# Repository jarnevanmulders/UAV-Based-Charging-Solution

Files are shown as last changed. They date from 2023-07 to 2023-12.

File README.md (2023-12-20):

# UAV Based Charging Solution

- [NRF52832 DK pinout](https://os.mbed.com/platforms/Nordic-nRF52-DK/)
- [NRF52832 DK schematics](https://devzone.nordicsemi.com/cfs-file/__key/communityserver-discussions-components-files/4/PCA10040_5F00_Schematic_5F00_And_5F00_PCB.pdf)

# HW design
- [BLE 2.4GHz antenna design](https://www.infineon.com/dgdl/Infineon-AN91445_Antenna_Design_and_RF_Layout_Guidelines-ApplicationNotes-v09_00-EN.pdf)

# Image hardware
Image measurement setup

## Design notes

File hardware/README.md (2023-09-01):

# Hardware status
## PRU
Working

Updates from v1.0 to v1.1
- I2C programmable load
- VDD_BLE directly connected to ADC pin P03 (without voltage divider)
- Additional RC filter after current limiter OPAMP
- Button from pull-up to pull down
- Additional filter (ferrite bead) on VDD_BLE supply line
- Other load switch implementation (with dual PMOS PMDPB55XP)
- Diode and shunt resistor location changed
- MIFA antenna tuning
  - Measured impedance 25+j25
    - Measured with R&S ZVL 3GHz VNA
    - Used a calibrated UFL connector cable (calibrated with ZVL one port calibration procedure)
    - Blank PCB board was used for measurement
  - Added 1.2 pF parallel with antenna (as compensation (see Smith V4.1))
  - Total [Pi] matching circuit (MCU - 0.8 pF capacitor - 3.9 nH inductor - 1.2 pF capacitor)

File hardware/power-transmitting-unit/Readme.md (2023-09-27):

## Hardware status

## Architecture
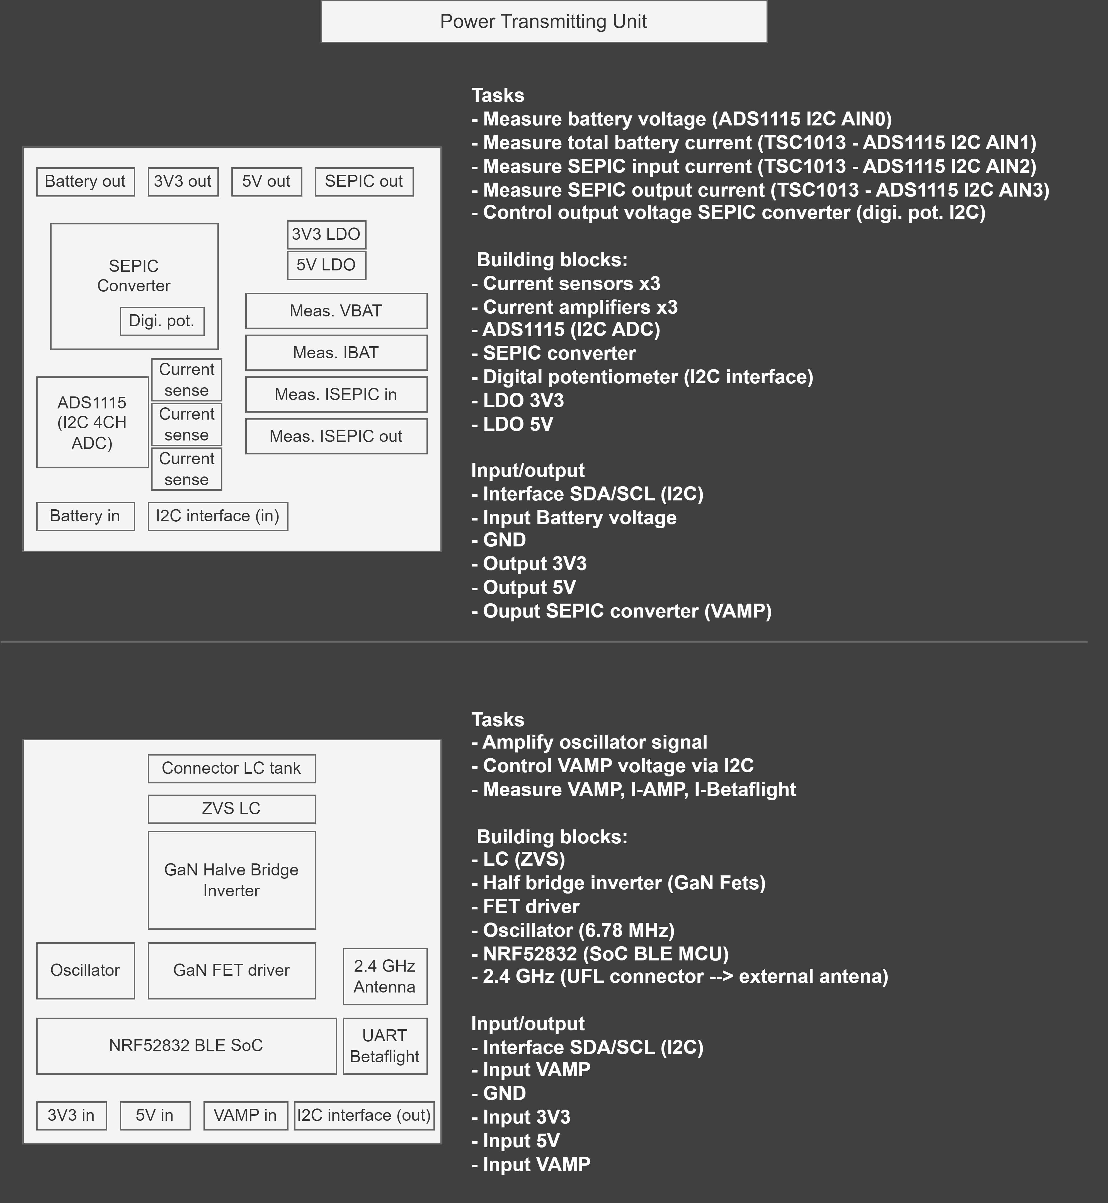
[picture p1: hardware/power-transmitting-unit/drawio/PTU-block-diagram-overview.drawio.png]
architecture


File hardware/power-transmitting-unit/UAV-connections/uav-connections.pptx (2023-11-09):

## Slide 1

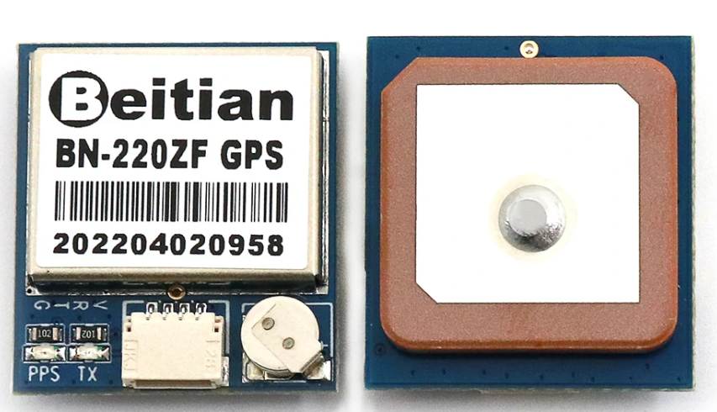
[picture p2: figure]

T1 – green
R1 – white
GND – black
5V – red

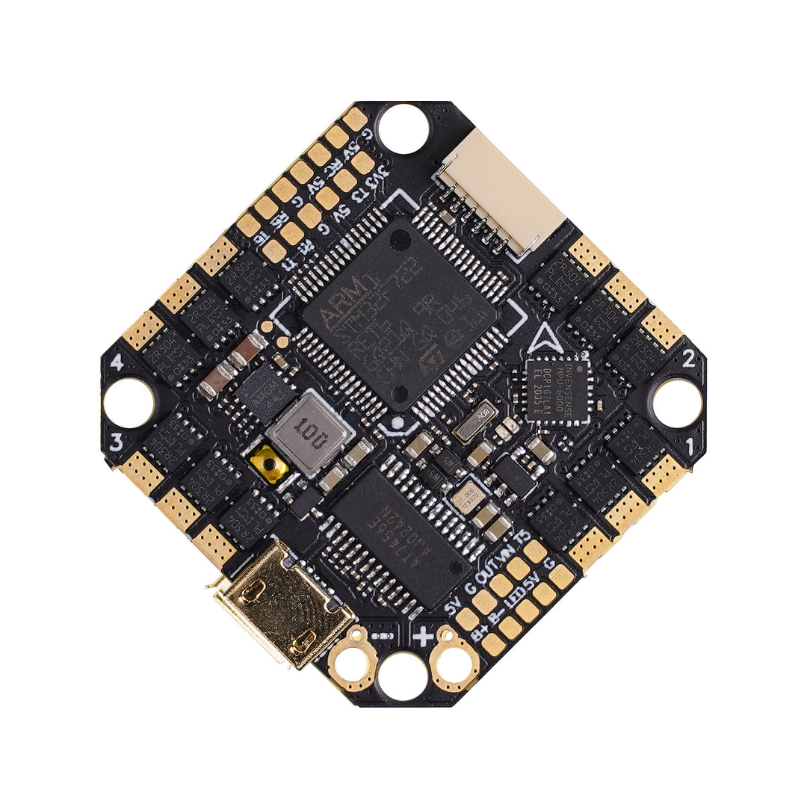
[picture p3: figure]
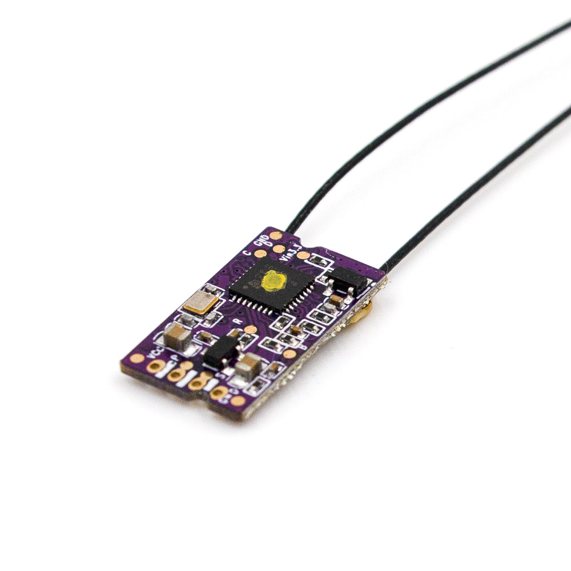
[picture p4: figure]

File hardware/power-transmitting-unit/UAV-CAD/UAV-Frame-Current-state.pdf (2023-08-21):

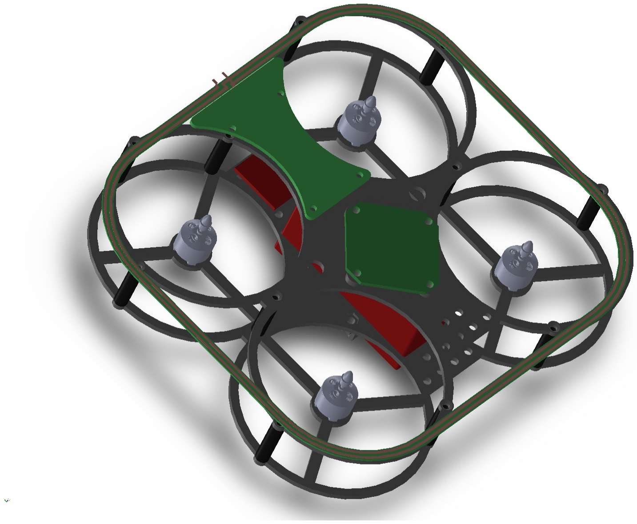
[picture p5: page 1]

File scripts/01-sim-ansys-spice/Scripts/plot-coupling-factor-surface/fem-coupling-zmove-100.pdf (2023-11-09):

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

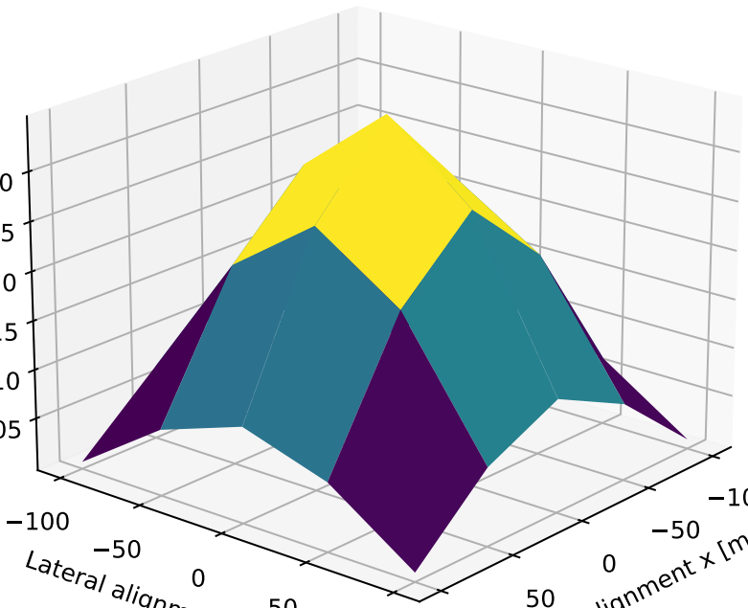
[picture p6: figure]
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

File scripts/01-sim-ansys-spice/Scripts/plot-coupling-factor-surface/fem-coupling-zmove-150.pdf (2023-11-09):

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

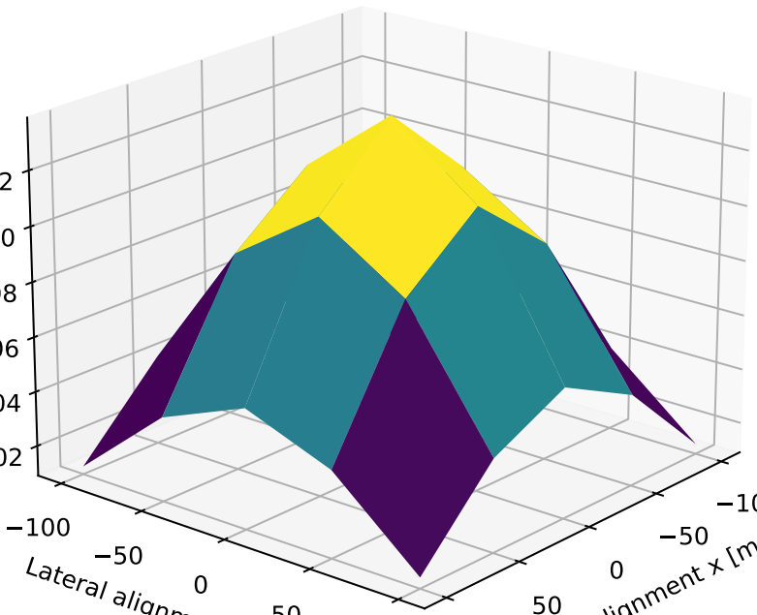
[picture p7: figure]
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

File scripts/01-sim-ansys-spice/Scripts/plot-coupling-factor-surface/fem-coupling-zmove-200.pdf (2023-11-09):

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

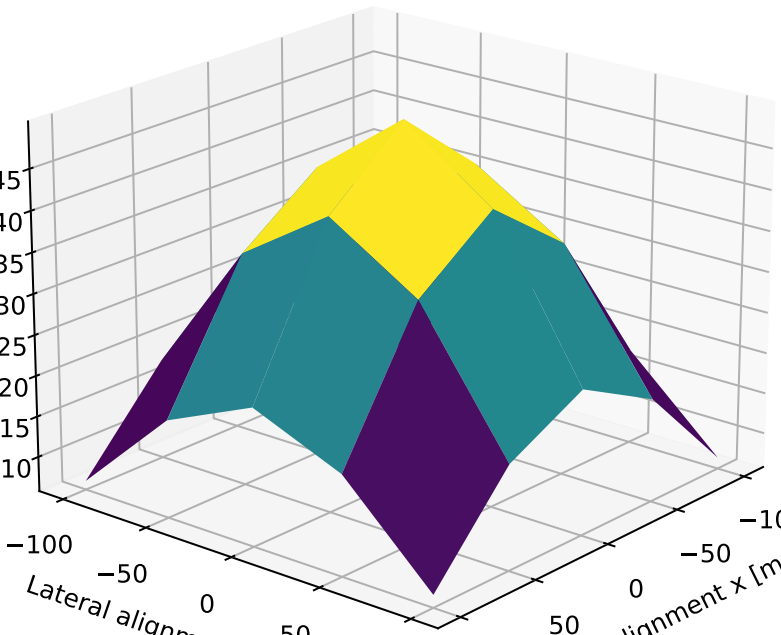
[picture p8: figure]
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

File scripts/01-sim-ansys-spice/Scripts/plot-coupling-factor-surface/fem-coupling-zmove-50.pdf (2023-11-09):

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

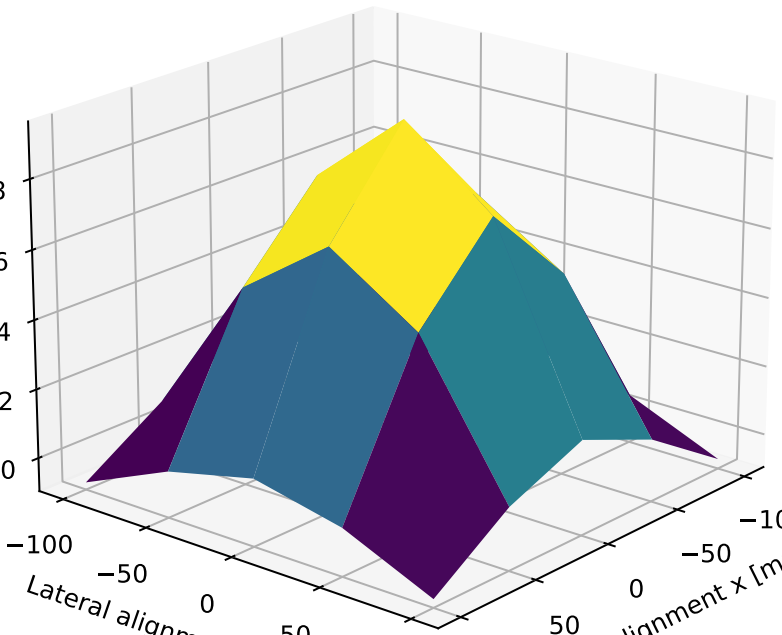
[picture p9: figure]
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

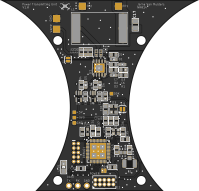
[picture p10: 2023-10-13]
hardware/power-transmitting-unit/Eagle-CAD/PTU-board/SVG-renders-design-1/top.png

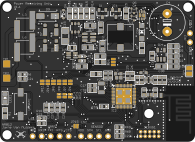
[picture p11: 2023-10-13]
hardware/power-receiving-unit/SVG-renders-design1-1/top.png

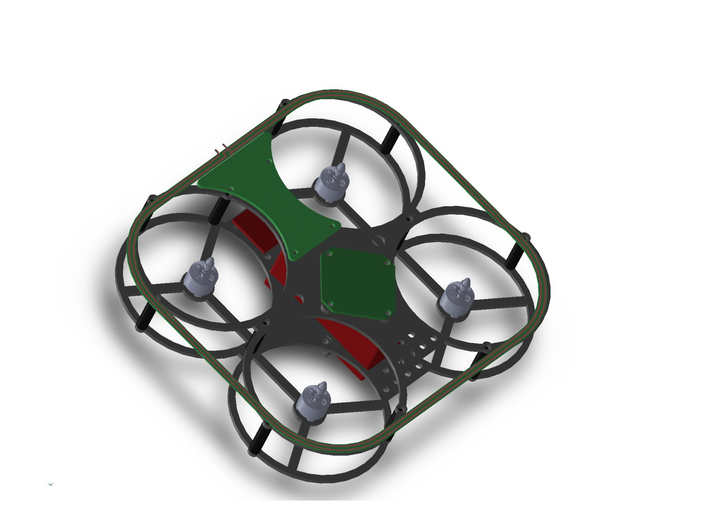
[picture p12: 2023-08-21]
hardware/power-transmitting-unit/UAV-CAD/UAV-Frame-Current-state-1.png

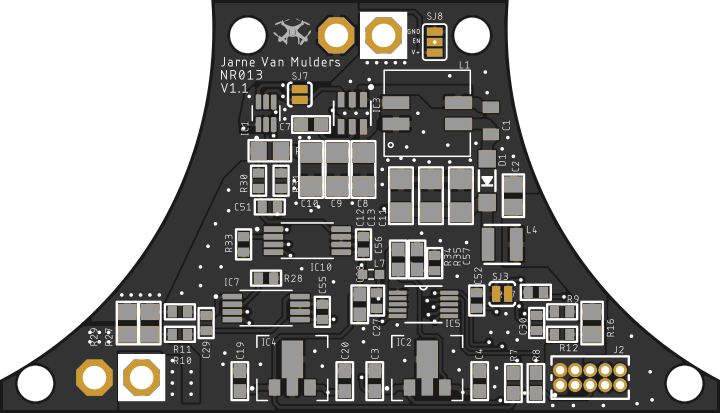
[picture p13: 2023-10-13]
hardware/power-transmitting-unit/Eagle-CAD/PSU-board/version-1-1/SVG-renders-design-1-1/top.png

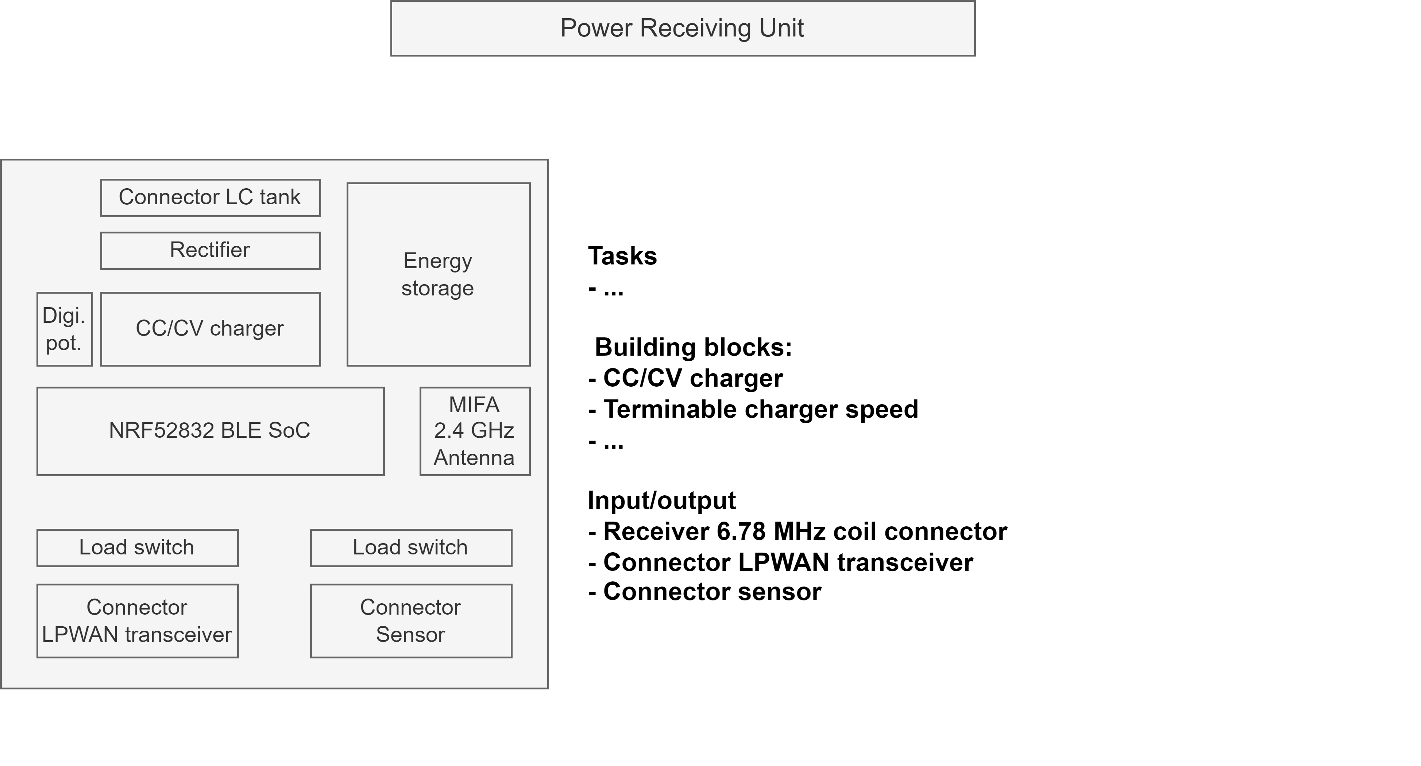
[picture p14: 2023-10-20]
hardware/power-receiving-unit/drawio/PRU-block-diagram-overview.drawio.png

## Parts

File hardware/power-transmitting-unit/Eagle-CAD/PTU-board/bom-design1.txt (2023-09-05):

Partlist exported from C:/Users/jarne/Documents/GitHub/IoT_energystorage_charger_ble/hardware/power-transmitting-unit/PTU-board/design1.sch at 05/09/2023 14:39

Part   Value                   Device                      Package                 Description                                                                                          AVAILABILITY DATASHEET-URL                                                DESCRIPTION                                                                            GENDER         IR MF                MOUNT MP                  PACKAGE                   PACKAGING PART-NUMBER   PINS PITCH  POPULARITY PRICE PROD_ID    PURCHASE-URL                                                     ROWS TP_SIGNAL_NAME TYPE     VALUE         WE-NUMBER                 Z    
C1     22p                     CAP_CERAMIC0402             0402                    Ceramic Capacitors                                                                                                                                                                                                                                                                                                                                                                                                                                                                                                                                                       
C2     22p                     CAP_CERAMIC0402             0402                    Ceramic Capacitors                                                                                                                                                                                                                                                                                                                                                                                                                                                                                                                                                       
C3     100n                    CAP_CERAMIC0402             0402                    Ceramic Capacitors                                                                                                                                                                                                                                                                                                                                                                                                                                                                                                                                                       
C4     100n                    CAP_CERAMIC0402             0402                    Ceramic Capacitors                                                                                                                                                                                                                                                                                                                                                                                                                                                                                                                                                       
C5     1u                      CAP_CERAMIC0402             0402                    Ceramic Capacitors                                                                                                                                                                                                                                                                                                                                                                                                                                                                                                                                                       
C6     22n                     CAP_CERAMIC0402             0402                    Ceramic Capacitors                                                                                                                                                                                                                                                                                                                                                                                                                                                                                                                                                       
C7     22n                     CAP_CERAMIC0402             0402                    Ceramic Capacitors                                                                                                                                                                                                                                                                                                                                                                                                                                                                                                                                                       
C8     1u                      CAP_CERAMIC0402             0402                    Ceramic Capacitors                                                                                                                                                                                                                                                                                                                                                                                                                                                                                                                                                       
C9     1u                      CAP_CERAMIC0402             0402                    Ceramic Capacitors                                                                                                                                                                                                                                                                                                                                                                                                                                                                                                                                                       
C10    1u                      CAP_CERAMIC0805             0805                    Ceramic Capacitors                                                                                                                                                                                                                                                                                                                                                                                                                                                                                                                                                       
C11    1u                      CAP_CERAMIC0805             0805                    Ceramic Capacitors                                                                                                                                                                                                                                                                                                                                                                                                                                                                                                                                                       
C12    1u                      CAP_CERAMIC0805             0805                    Ceramic Capacitors                                                                                                                                                                                                                                                                                                                                                                                                                                                                                                                                                       
C13    1u                      CAP_CERAMIC0805             0805                    Ceramic Capacitors                                                                                                                                                                                                                                                                                                                                                                                                                                                                                                                                                       
C14    10n                     CAP_CERAMIC0402             0402                    Ceramic Capacitors                                                                                                                                                                                                                                                                                                                                                                                                                                                                                                                                                       
C15    10n                     CAP_CERAMIC0402             0402                    Ceramic Capacitors                                                                                                                                                                                                                                                                                                                                                                                                                                                                                                                                                       
C16    10n                     CAP_CERAMIC0402             0402                    Ceramic Capacitors                                                                                                                                                                                                                                                                                                                                                                                                                                                                                                                                                       
C17    1u                      CAP_CERAMIC0805             0805                    Ceramic Capacitors                                                                                                                                                                                                                                                                                                                                                                                                                                                                                                                                                       
C18    100n                    CAP_CERAMIC0603             0603                    Ceramic Capacitors                                                                                                                                                                                                                                                                                                                                                                                                                                                                                                                                                       
C21    100n                    CAP_CERAMIC0402             0402                    Ceramic Capacitors                                                                                                                                                                                                                                                                                                                                                                                                                                                                                                                                                       
C22    100n                    CAP_CERAMIC0402             0402                    Ceramic Capacitors                                                                                                                                                                                                                                                                                                                                                                                                                                                                                                                                                       
C31    4u7                     CAP_CERAMIC0603             0603                    Ceramic Capacitors                                                                                                                                                                                                                                                                                                                                                                                                                                                                                                                                                       
C32    100n                    CAP_CERAMIC0402             0402                    Ceramic Capacitors                                                                                                                                                                                                                                                                                                                                                                                                                                                                                                                                                       
C33    100n                    CAP_CERAMIC0402             0402                    Ceramic Capacitors                                                                                                                                                                                                                                                                                                                                                                                                                                                                                                                                                       
C34    100n                    CAP_CERAMIC0402             0402                    Ceramic Capacitors                                                                                                                                                                                                                                                                                                                                                                                                                                                                                                                                                       
C35    DNP                     CAP_CERAMIC0402             0402                    Ceramic Capacitors                                                                                                                                                                                                                                                                                                                                                                                                                                                                                                                                                       
C36    100p                    CAP_CERAMIC0402             0402                    Ceramic Capacitors                                                                                                                                                                                                                                                                                                                                                                                                                                                                                                                                                       
C37    1u                      CAP_CERAMIC0402             0402                    Ceramic Capacitors                                                                                                                                                                                                                                                                                                                                                                                                                                                                                                                                                       
C40    6p                      CAP_CERAMIC0402             0402                    Ceramic Capacitors                                                                                                                                                                                                                                                                                                                                                                                                                                                                                                                                                       
C41    6p                      CAP_CERAMIC0402             0402                    Ceramic Capacitors                                                                                                                                                                                                                                                                                                                                                                                                                                                                                                                                                       
C43    100n                    CAP_CERAMIC0402             0402                    Ceramic Capacitors                                                                                                                                                                                                                                                                                                                                                                                                                                                                                                                                                       
C44    DNP                     CAP_CERAMIC0402             0402                    Ceramic Capacitors                                                                                                                                                                                                                                                                                                                                                                                                                                                                                                                                                       
C45    0.8p                    CAP_CERAMIC0402             0402                    Ceramic Capacitors                                                                                                                                                                                                                                                                                                                                                                                                                                                                                                                                                       
D1     BAT54K                  DIODESOD-523                SOD-523                 Diode                                                                                                                                                                                                                                                                                                                                                                                                                                                                                                                                                                    
D2     RB751S40T1G             DIODESOD-523                SOD-523                 Diode                                                                                                                                                                                                                                                                                                                                                                                                                                                                                                                                                                    
D3     RB751S40T1G             DIODESOD-523                SOD-523                 Diode                                                                                                                                                                                                                                                                                                                                                                                                                                                                                                                                                                    
D4     CZRU52C5V1              CZRU52                      SOD-523F                                                                                                                                                                                                                                                                                                                                                                                                                                                                                                                                                                                         
D5     RB751S40T1G             DIODESOD-523                SOD-523                 Diode                                                                                                                                                                                                                                                                                                                                                                                                                                                                                                                                                                    
D6     RB751S40T1G             DIODESOD-523                SOD-523                 Diode                                                                                                                                                                                                                                                                                                                                                                                                                                                                                                                                                                    
DEBUG1 CORTEX_DEBUGPTH         CORTEX_DEBUGPTH             2X5-PTH-1.27MM          Cortex Debug Connector                                                                                                                                                                                                                                                                                                                                                                                                                                                                                                                                                   
FET1   EPC8010                 EPC8010                     BGA-8010                                                                                                                                                                                                                                                                                                                                                                                                                                                                                                                                                                                         
FET2   EPC8010                 EPC8010                     BGA-8010                                                                                                                                                                                                                                                                                                                                                                                                                                                                                                                                                                                         
FET3   EPC2038                 EPC2038                     BGA-2038                                                                                                                                                                                                                                                                                                                                                                                                                                                                                                                                                                                         
IC1    LM5113SDX/NOPB          LM5113SDX/NOPB              SON80P400X400X80-11N    5A, 100V Half-Bridge Gate Driver for Enhancement Mode GaN FETs 10-WSON -40 to 125 Check availability In Stock                                                                   1.2-A/5-A, 100-V half bridge gate driver for GaNFET 10-WSON -40 to 125                                  Texas Instruments       LM5113SDX/NOPB      WSON-10 Texas Instruments                                                None             https://pricing.snapeda.com/search?q=LM5113SDX/NOPB&ref=eda                                                                                
IC2    NRF52832                NRF52832-EXTENDED           QFN48-6X6MM-EXTENDED                                                                                                                                                                                                                                                                                                                                                                                                                                                                                                                                                                             
IC3    DSC1001DI2-006.7800     DSC1001DI2-006.7800         2.5X2.0MMPLASTICPACKAGE None Check availability                                                                              In Stock                                                                   25 MHz XO (Standard) CMOS Oscillator 1.8V ~ 3.3V Standby (Power Down) 4-SMD, No Lead                    Microchip               DSC1001DI1-025.0000 SMD-4 Microchip                                                          None             https://pricing.snapeda.com/search?q=DSC1001DI1-025.0000&ref=eda
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

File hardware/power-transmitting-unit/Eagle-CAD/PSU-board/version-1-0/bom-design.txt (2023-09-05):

Partlist exported from C:/Users/jarne/Documents/GitHub/IoT_energystorage_charger_ble/hardware/power-transmitting-unit/PSU-board/design.sch at 05/09/2023 14:34

Part Value             Device                           Package             Description                                                   AVAILABILITY CHECK_PRICES                                                                       DATASHEET-URL                                           DESCRIPTION                                                                                                                               GENDER     IR MF                MOUNT MP                PACKAGE                      PACKAGING PART-NUMBER   PINS PITCH  PRICE PURCHASE-URL                                                 ROWS SNAPEDA_LINK                                                                        TYPE     VALUE         WE-NUMBER                
C1   1u                WCAP-CSGP_0805_885012207103_WAVE WCAP-CSGP_0805_WAVE WCAP-CSGP Ceramic Capacitors                                                                                                                                                                                                                                                                                                                                                                                                                                                                                                                                                                                                                                                                         
C2   10u               CAP_CERAMIC0805                  0805                Ceramic Capacitors                                                                                                                                                                                                                                                                                                                                                                                                                                                                                                                                                                                                                                                                                   
C3   10u               CAP_CERAMIC0603                  0603                Ceramic Capacitors                                                                                                                                                                                                                                                                                                                                                                                                                                                                                                                                                                                                                                                                                   
C4   10u               CAP_CERAMIC0603                  0603                Ceramic Capacitors                                                                                                                                                                                                                                                                                                                                                                                                                                                                                                                                                                                                                                                                                   
C5   100n              CAP_CERAMIC0402                  0402                Ceramic Capacitors                                                                                                                                                                                                                                                                                                                                                                                                                                                                                                                                                                                                                                                                                   
C7   1u                CAP_CERAMIC0603                  0603                Ceramic Capacitors                                                                                                                                                                                                                                                                                                                                                                                                                                                                                                                                                                                                                                                                                   
C8   10u               CAP_CERAMIC1206                  1206                Ceramic Capacitors                                                                                                                                                                                                                                                                                                                                                                                                                                                                                                                                                                                                                                                                                   
C9   10u               CAP_CERAMIC1206                  1206                Ceramic Capacitors                                                                                                                                                                                                                                                                                                                                                                                                                                                                                                                                                                                                                                                                                   
C10  10u               CAP_CERAMIC1206                  1206                Ceramic Capacitors                                                                                                                                                                                                                                                                                                                                                                                                                                                                                                                                                                                                                                                                                   
C11  10u               CAP_CERAMIC1206                  1206                Ceramic Capacitors                                                                                                                                                                                                                                                                                                                                                                                                                                                                                                                                                                                                                                                                                   
C12  10u               CAP_CERAMIC1206                  1206                Ceramic Capacitors                                                                                                                                                                                                                                                                                                                                                                                                                                                                                                                                                                                                                                                                                   
C13  10u               CAP_CERAMIC1206                  1206                Ceramic Capacitors                                                                                                                                                                                                                                                                                                                                                                                                                                                                                                                                                                                                                                                                                   
C19  10u               CAP_CERAMIC0603                  0603                Ceramic Capacitors                                                                                                                                                                                                                                                                                                                                                                                                                                                                                                                                                                                                                                                                                   
C20  10u               CAP_CERAMIC0603                  0603                Ceramic Capacitors                                                                                                                                                                                                                                                                                                                                                                                                                                                                                                                                                                                                                                                                                   
C27  100n              CAP_CERAMIC0402                  0402                Ceramic Capacitors                                                                                                                                                                                                                                                                                                                                                                                                                                                                                                                                                                                                                                                                                   
C28  10u               CAP_CERAMIC0603                  0603                Ceramic Capacitors                                                                                                                                                                                                                                                                                                                                                                                                                                                                                                                                                                                                                                                                                   
C29  100n              CAP_CERAMIC0402                  0402                Ceramic Capacitors                                                                                                                                                                                                                                                                                                                                                                                                                                                                                                                                                                                                                                                                                   
C30  100n              CAP_CERAMIC0402                  0402                Ceramic Capacitors                                                                                                                                                                                                                                                                                                                                                                                                                                                                                                                                                                                                                                                                                   
C51  100n              CAP_CERAMIC0402                  0402                Ceramic Capacitors                                                                                                                                                                                                                                                                                                                                                                                                                                                                                                                                                                                                                                                                                   
C52  100n              CAP_CERAMIC0402                  0402                Ceramic Capacitors                                                                                                                                                                                                                                                                                                                                                                                                                                                                                                                                                                                                                                                                                   
C55  100n              CAP_CERAMIC0402                  0402                Ceramic Capacitors                                                                                                                                                                                                                                                                                                                                                                                                                                                                                                                                                                                                                                                                                   
C56  100n              CAP_CERAMIC0402                  0402                Ceramic Capacitors                                                                                                                                                                                                                                                                                                                                                                                                                                                                                                                                                                                                                                                                                   
C57  100n              CAP_CERAMIC0402                  0402                Ceramic Capacitors
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

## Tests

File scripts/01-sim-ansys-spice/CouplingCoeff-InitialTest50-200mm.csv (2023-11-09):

Freq [MHz] | zmove [mm] | Matrix1.CplCoef(TX_in,RX_in) [] | Matrix1.L(RX_in,RX_in) [uH] | Matrix1.L(TX_in,TX_in) [uH] | Matrix1.R(RX_in,RX_in) [mOhm] | Matrix1.R(TX_in,TX_in) [mOhm]
6.78 | 50 | nan | nan | nan | nan | nan
6.78 | 100 | 0.0333610847908959 | 3.66828225855419 | 2.2581492463435 | 602.7788268 | 487.0617835
6.78 | 150 | 0.0131339871884984 | 3.64405427781074 | 2.26005545967039 | 601.0554673 | 484.7673939
6.78 | 200 | 0.00464744356723928 | 3.6750234535271 | 2.3240408525049 | 602.6356695 | 486.7066287

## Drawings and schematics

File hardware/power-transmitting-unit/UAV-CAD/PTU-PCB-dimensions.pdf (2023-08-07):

E E

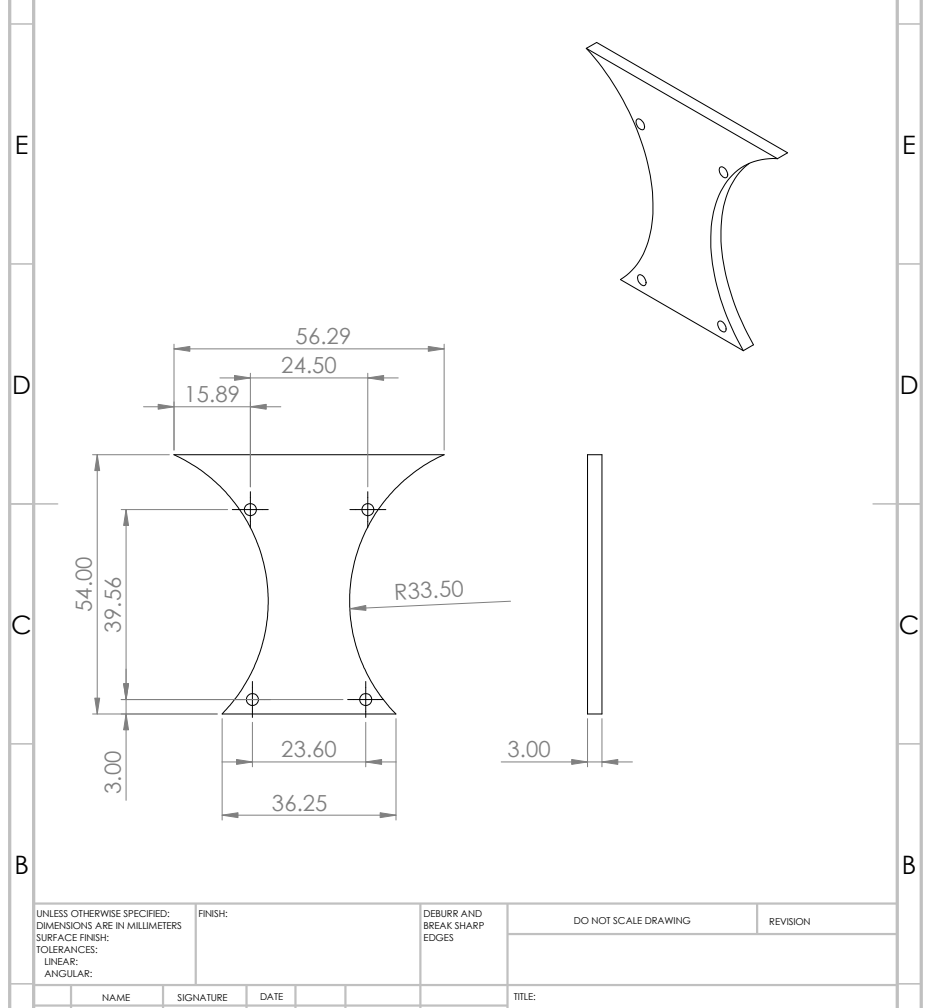
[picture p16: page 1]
TITLE:; DO NOT SCALE DRAWING; REVISION; FINISH:; EDGES; NAME; SIGNATURE; DATE; DEBURR AND BREAK SHARP

UNLESS OTHERWISE SPECIFIED:
DIMENSIONS ARE IN MILLIMETERS
SURFACE FINISH:
TOLERANCES:
LINEAR:
ANGULAR:

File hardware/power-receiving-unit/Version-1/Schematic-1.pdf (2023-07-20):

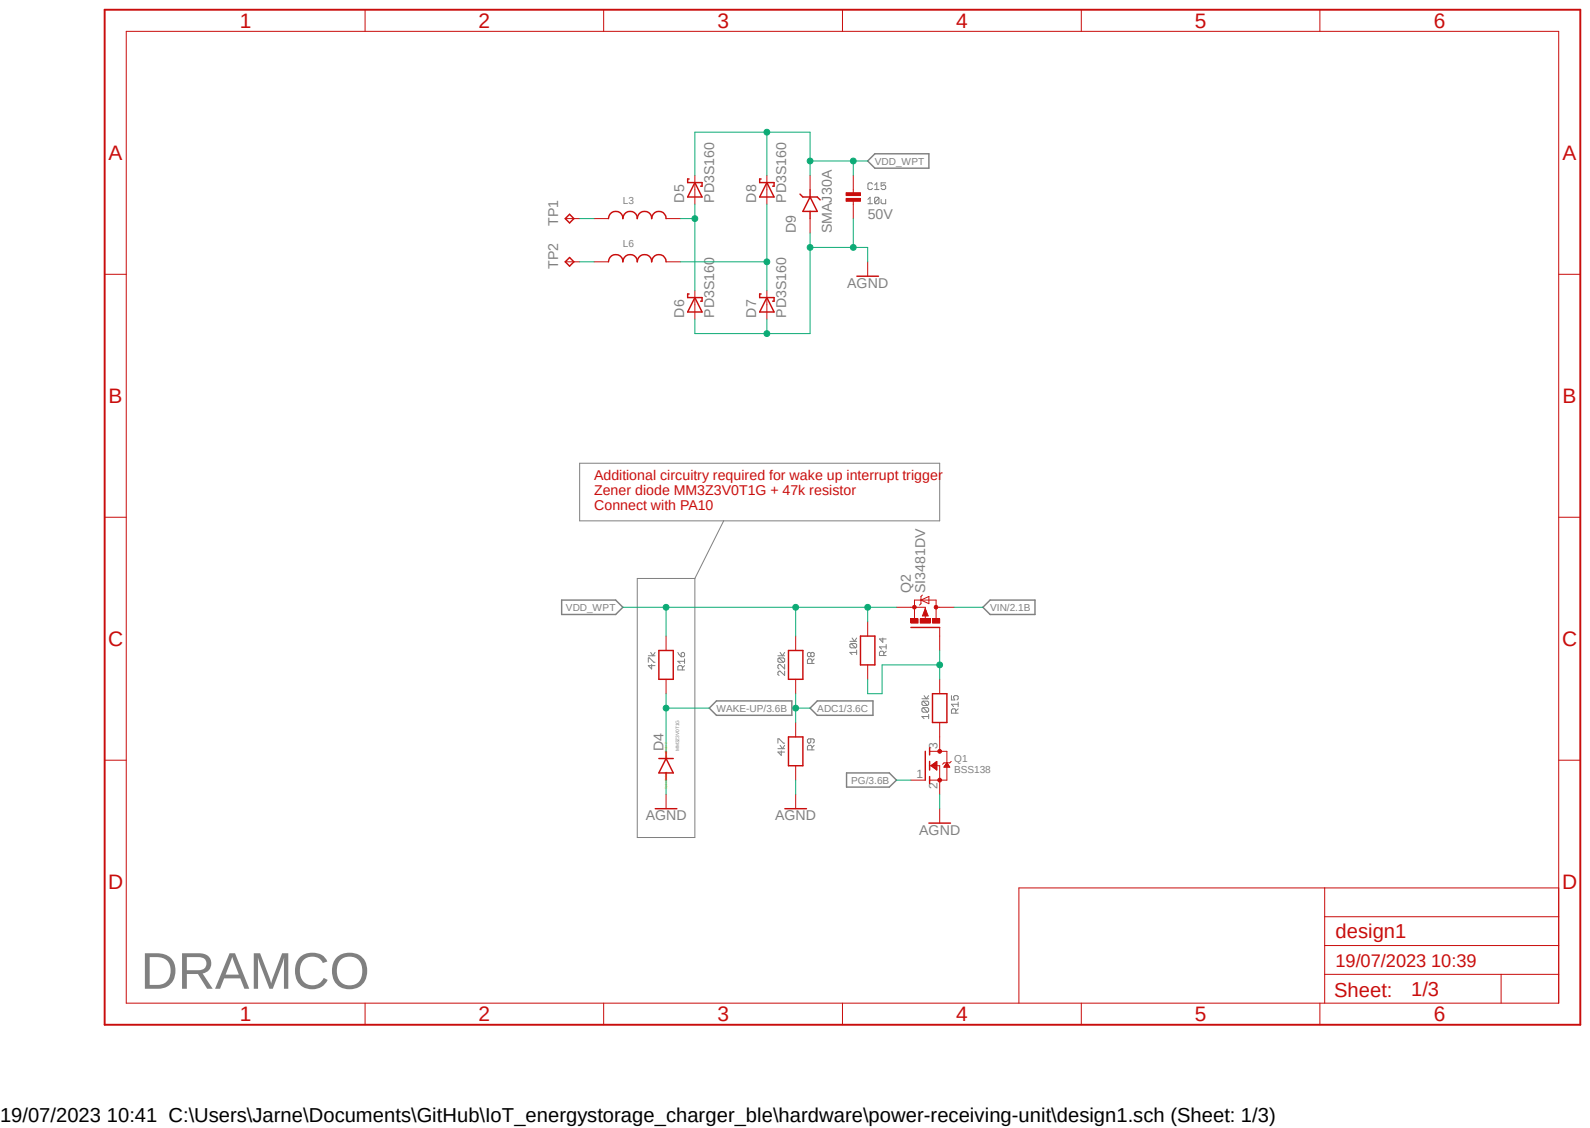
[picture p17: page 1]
19/07/2023 10:41 C:\Users\Jarne\Documents\GitHub\IoT_energystorage_charger_ble\hardware\power-receiving-unit\design1.sch (Sheet: 1/3) SpiceOrder 1 SpiceOrder 2; BSS138 SI3481DV MM³Z3V⁰T1G; PD³S¹⁶⁰ PD³S¹⁶⁰; SMAJ30A; AGND; DRAMCO; D⁹TP¹ TP²; VIN/2.1B; WAKE-UP/3.6B; ADC1/3.6C; VDD_WPT; Sheet:; design1

Additional circuitry required for wake up interrupt trigger
Zener diode MM3Z3V0T1G + 47k resistor
Connect with PA10

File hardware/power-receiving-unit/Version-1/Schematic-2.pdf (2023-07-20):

A

A

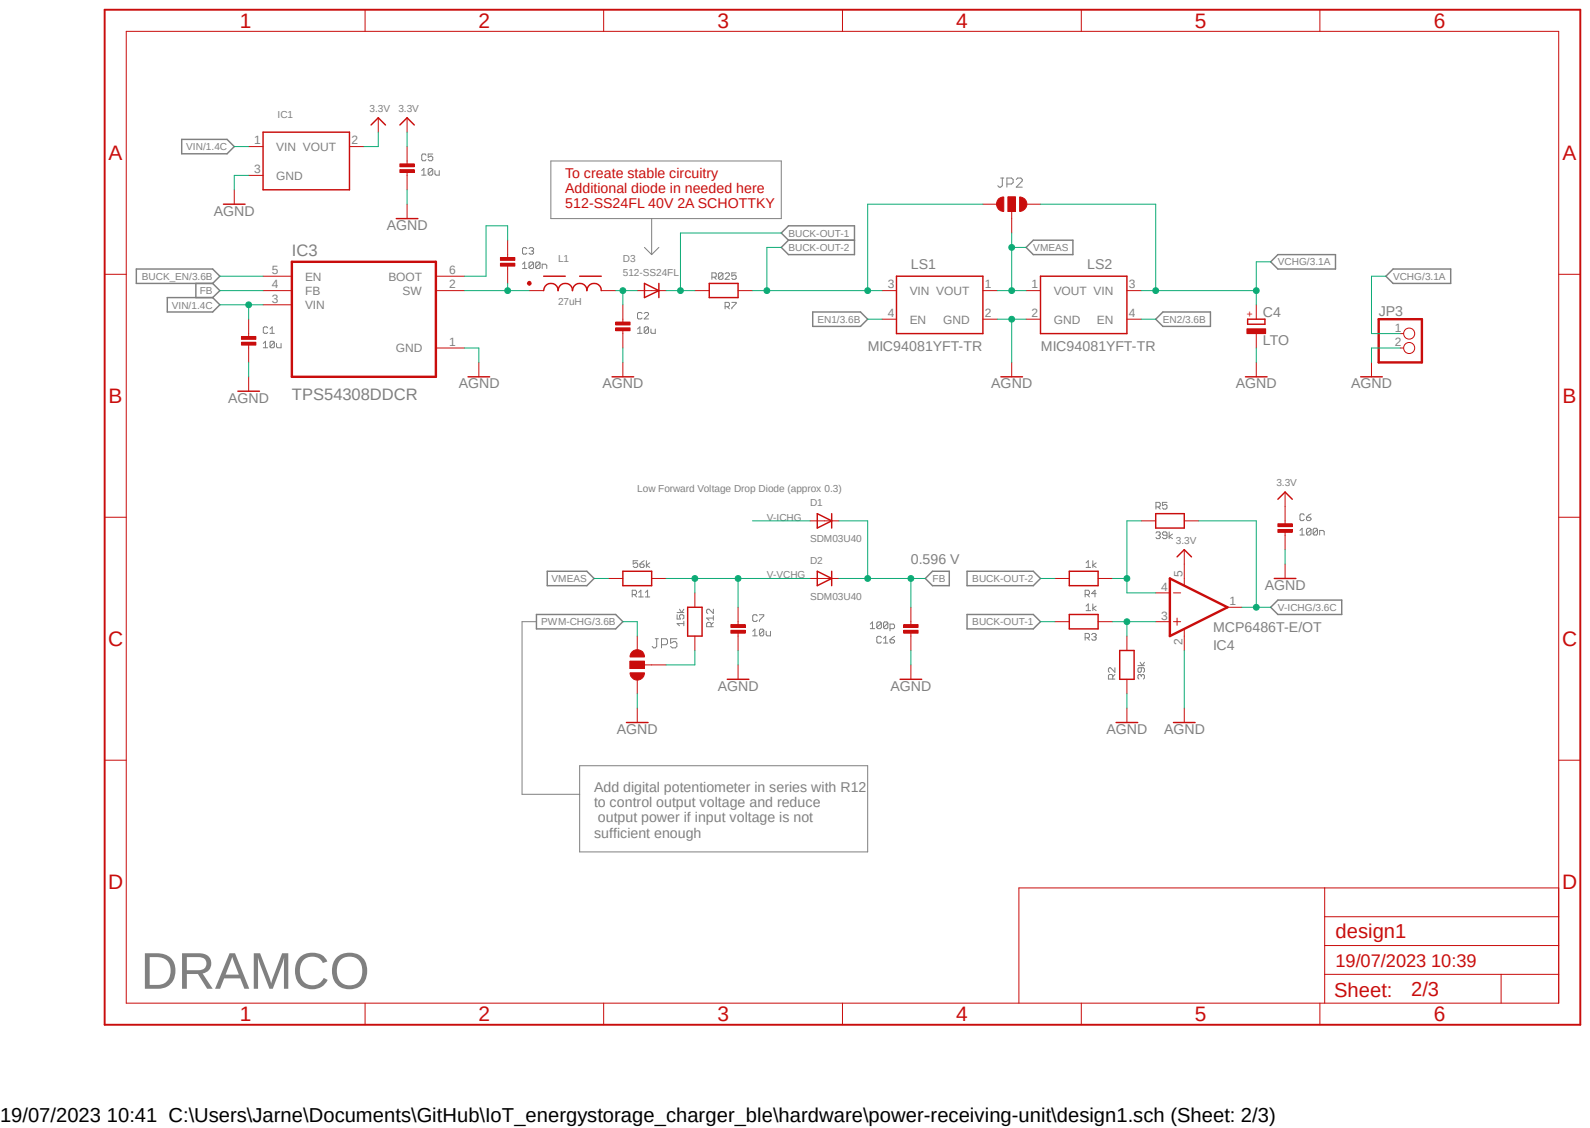
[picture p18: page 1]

To create stable circuitry
Additional diode in needed here
512-SS24FL 40V 2A SCHOTTKY

Low Forward Voltage Drop Diode (approx 0.3)

Add digital potentiometer in series with R12
to control output voltage and reduce
output power if input voltage is not
sufficient enough

19/07/2023 10:41 C:\Users\Jarne\Documents\GitHub\IoT_energystorage_charger_ble\hardware\power-receiving-unit\design1.sch (Sheet: 2/3)

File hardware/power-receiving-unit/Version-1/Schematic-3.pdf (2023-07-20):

## Pin

## Pin

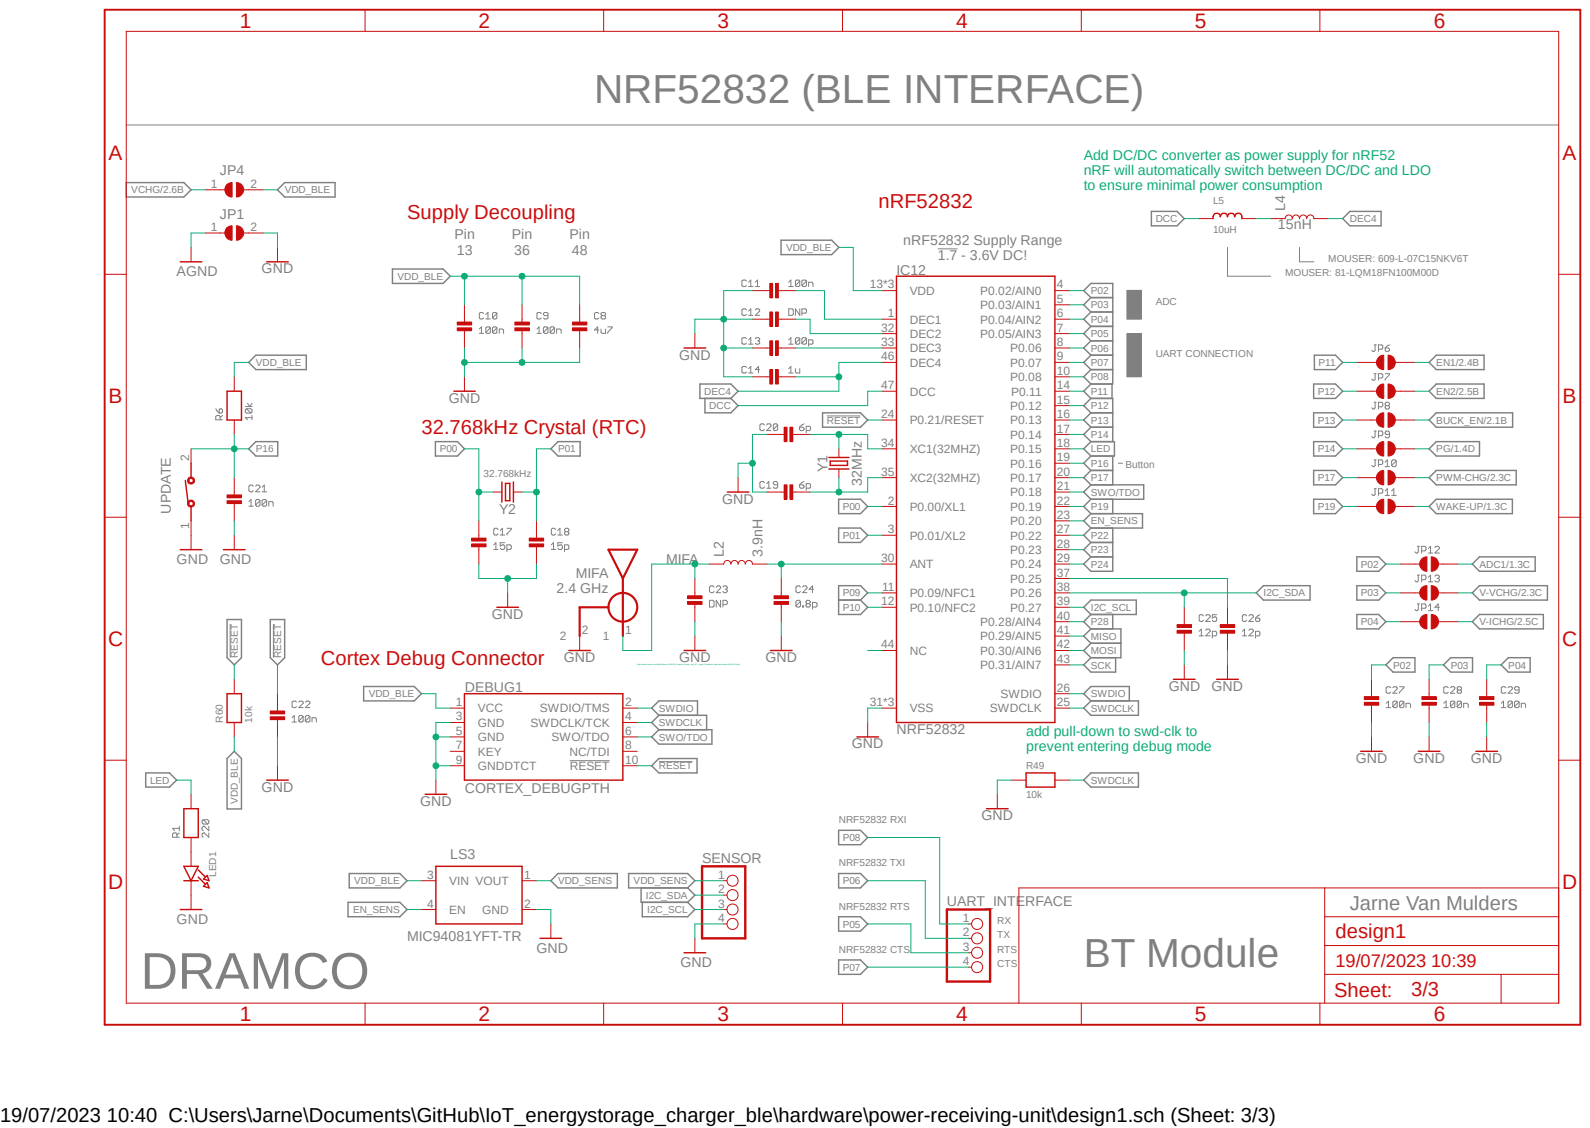
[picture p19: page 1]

Add DC/DC converter as power supply for nRF52
nRF will automatically switch between DC/DC and LDO
to ensure minimal power consumption

https://www.infineon.com/dgdl/Infineon-AN91445_Antenna_Design_and_RF_Layout_Guidelines-ApplicationNotes-v09_00-EN.pdf

add pull-down to swd-clk to
prevent entering debug mode

19/07/2023 10:40 C:\Users\Jarne\Documents\GitHub\IoT_energystorage_charger_ble\hardware\power-receiving-unit\design1.sch (Sheet: 3/3)

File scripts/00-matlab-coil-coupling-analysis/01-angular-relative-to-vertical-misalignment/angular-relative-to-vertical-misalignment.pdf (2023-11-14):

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

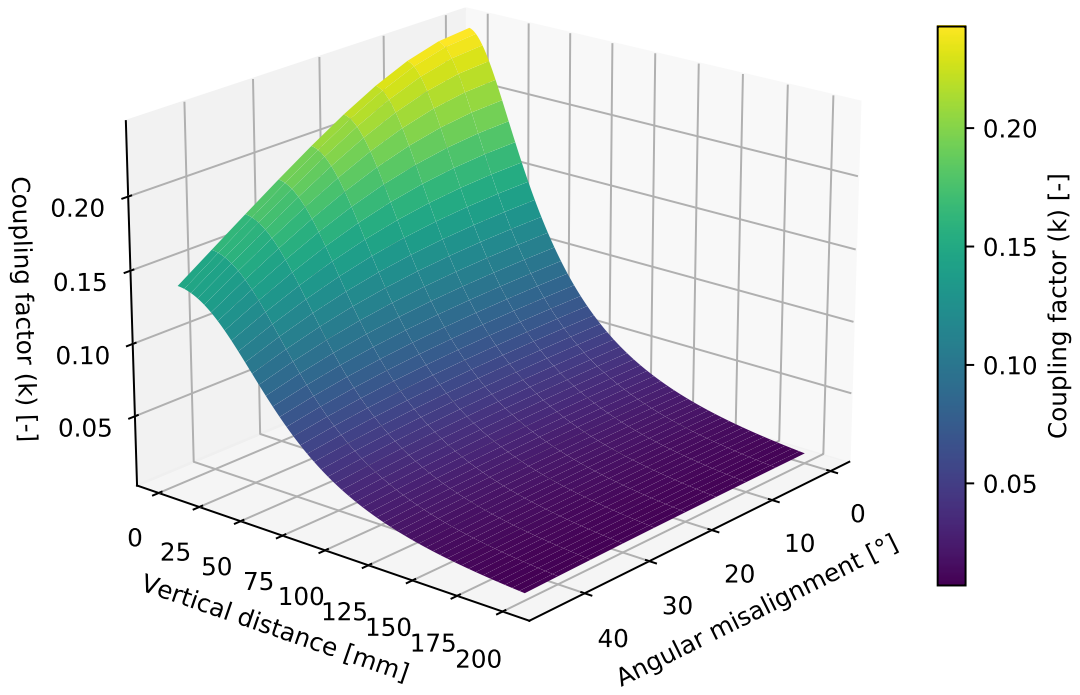
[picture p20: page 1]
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

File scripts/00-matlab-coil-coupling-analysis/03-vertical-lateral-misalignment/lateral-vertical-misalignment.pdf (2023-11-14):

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

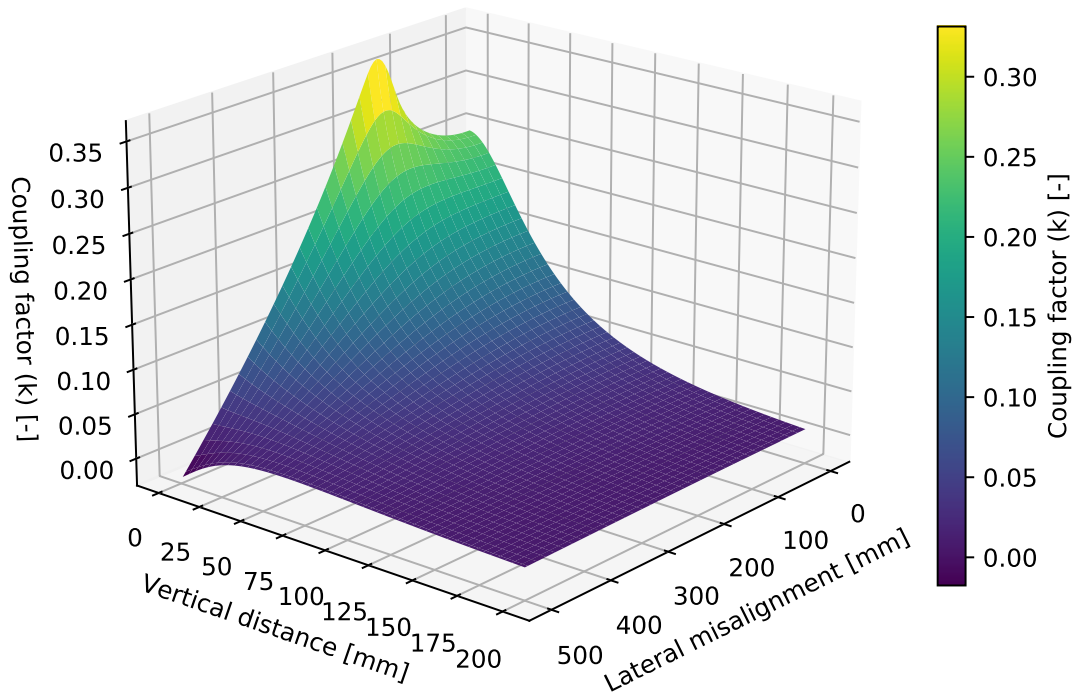
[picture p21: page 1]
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

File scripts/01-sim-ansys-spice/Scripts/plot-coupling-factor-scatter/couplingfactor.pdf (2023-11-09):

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

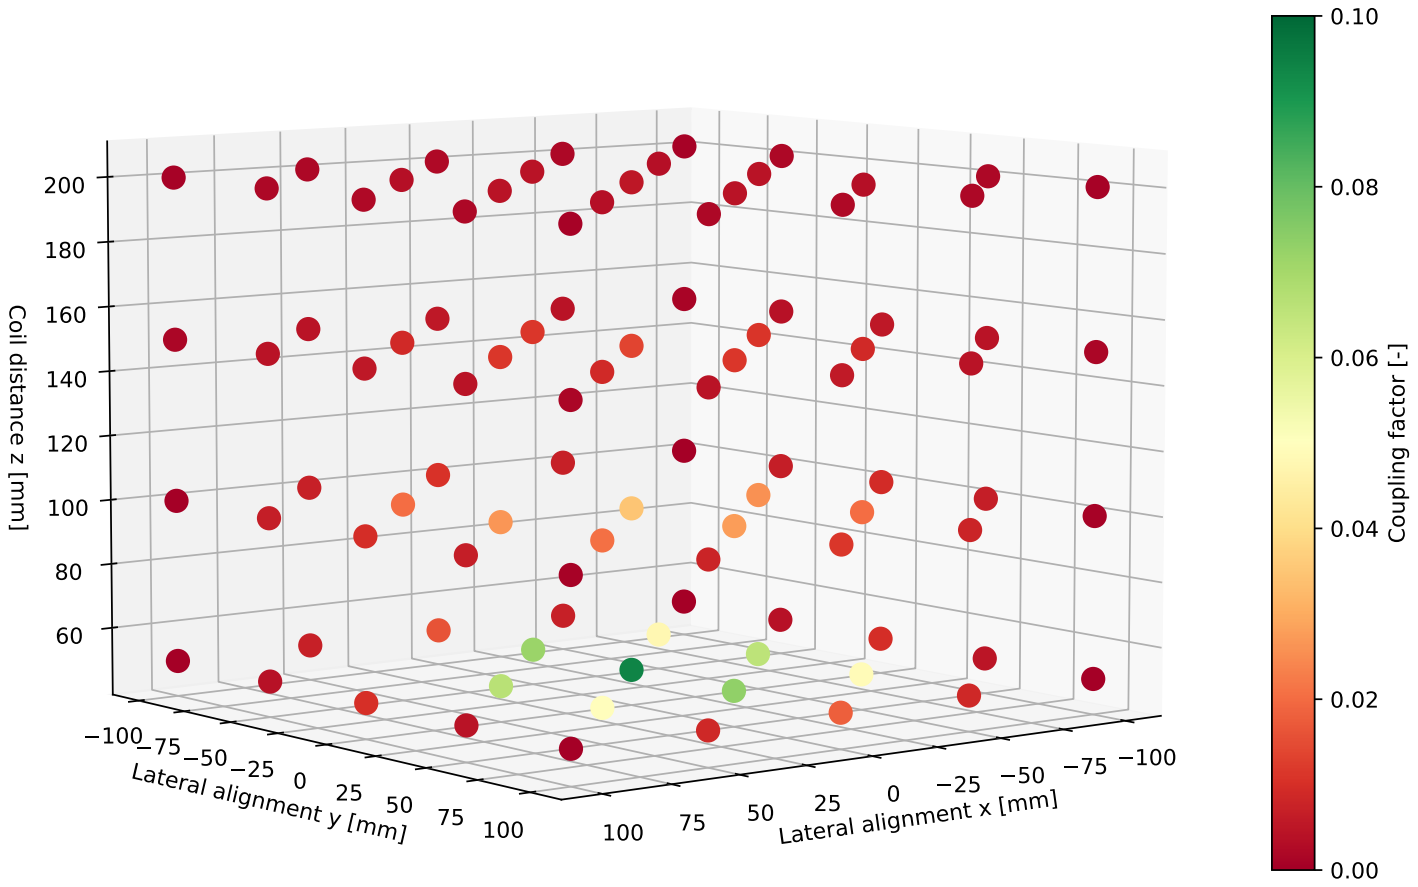
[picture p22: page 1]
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

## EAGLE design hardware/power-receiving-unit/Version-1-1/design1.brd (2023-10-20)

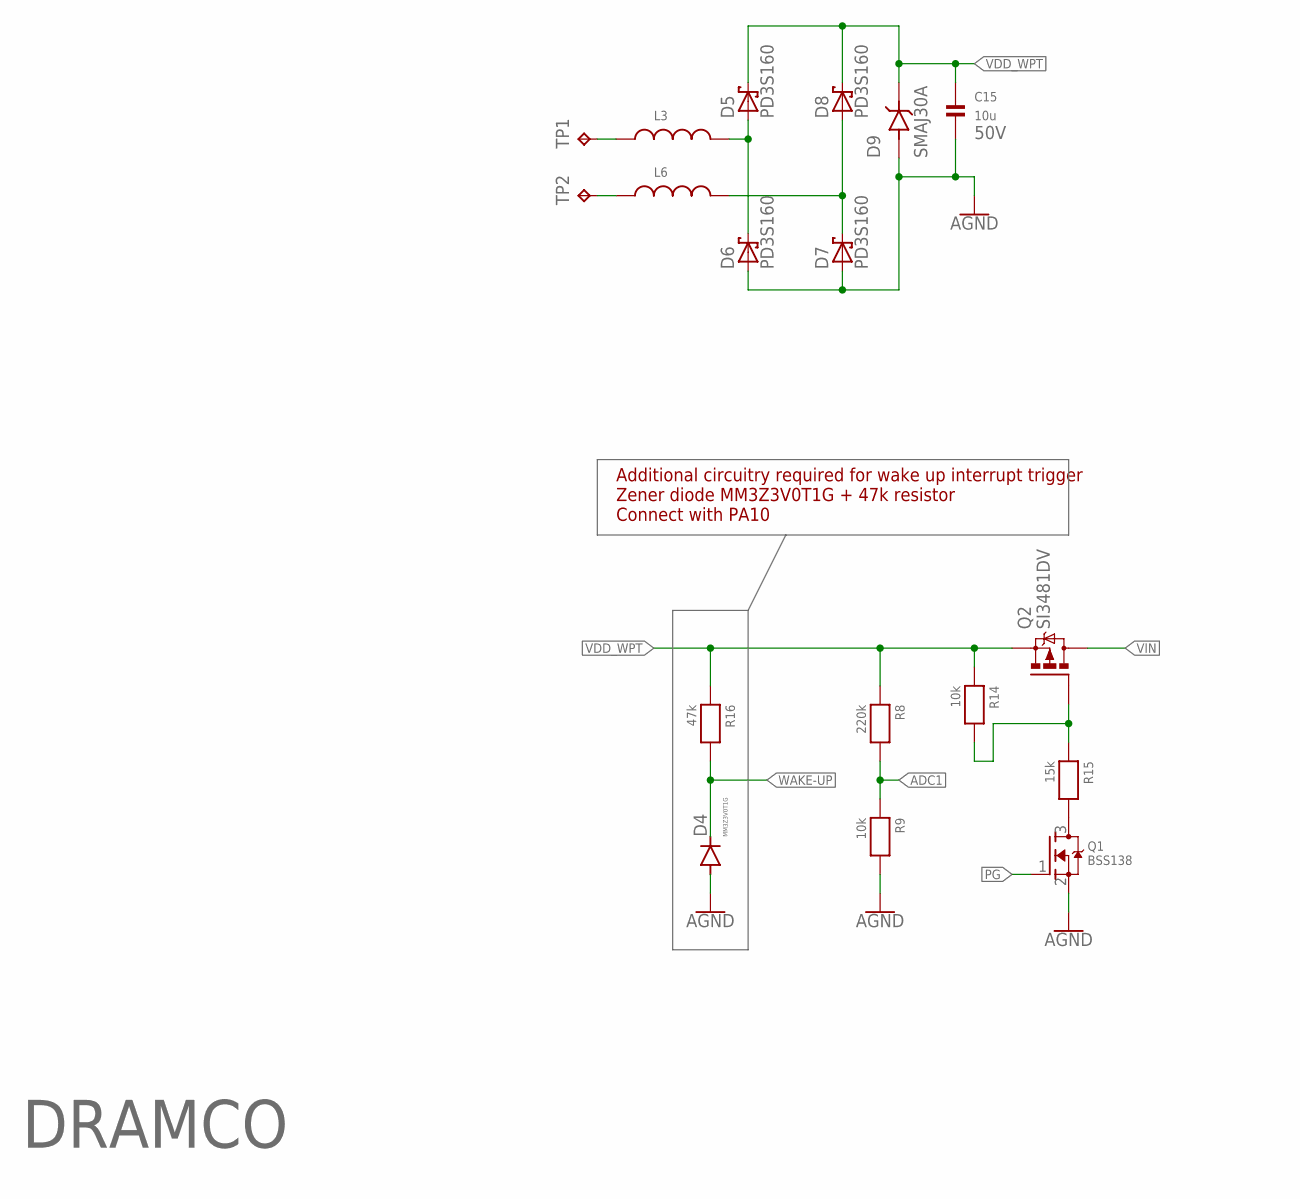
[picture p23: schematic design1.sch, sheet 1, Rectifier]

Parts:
C15: 10u; 1206
D4: MM3Z3V0T1G; SOD323-R
D5, D6, D7, D8: PD3S160; POWERDI323
D9: SMAJ30A; DIOM5026X229N
L3, L6: WE-CAIR_4248_744912182; WE-CAIR_4248
Q1: BSS138; SOT23-R
Q2: SI3481DV; TSOP-6.PAC
R8: 220k; 0603
R9, R14: 10k; 0603
R15: 15k; 0603
R16: 47k; 0603
TP1, TP2: TPTP20SQ; TP20SQ

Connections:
ADC1: R8.2, R9.1; also elsewhere on the board
AGND: C15.2, D4.A, D6.A, D7.A, D9.A, Q1.2 (S), R9.2; also elsewhere on the board
unnamed: Q1.3 (D), R15.2
unnamed: Q2.3 (G), R14.2, R15.1
unnamed: L6.1, TP2.TP
unnamed: L3.1, TP1.TP
unnamed: D5.A, D6.C, L3.2
unnamed: D7.C, D8.A, L6.2
PG: Q1.1 (G); also elsewhere on the board
VDD_WPT: C15.1, D5.C, D8.C, D9.C, Q2.4 (S), R8.1, R14.1, R16.1
VIN: Q2.1 (D), Q2.2 (D), Q2.5 (D), Q2.6 (D); also elsewhere on the board
WAKE-UP: D4.C, R16.2; also elsewhere on the board

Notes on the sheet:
Additional circuitry required for wake up interrupt trigger Zener diode MM3Z3V0T1G + 47k resistor Connect with PA10
50V
DRAMCO

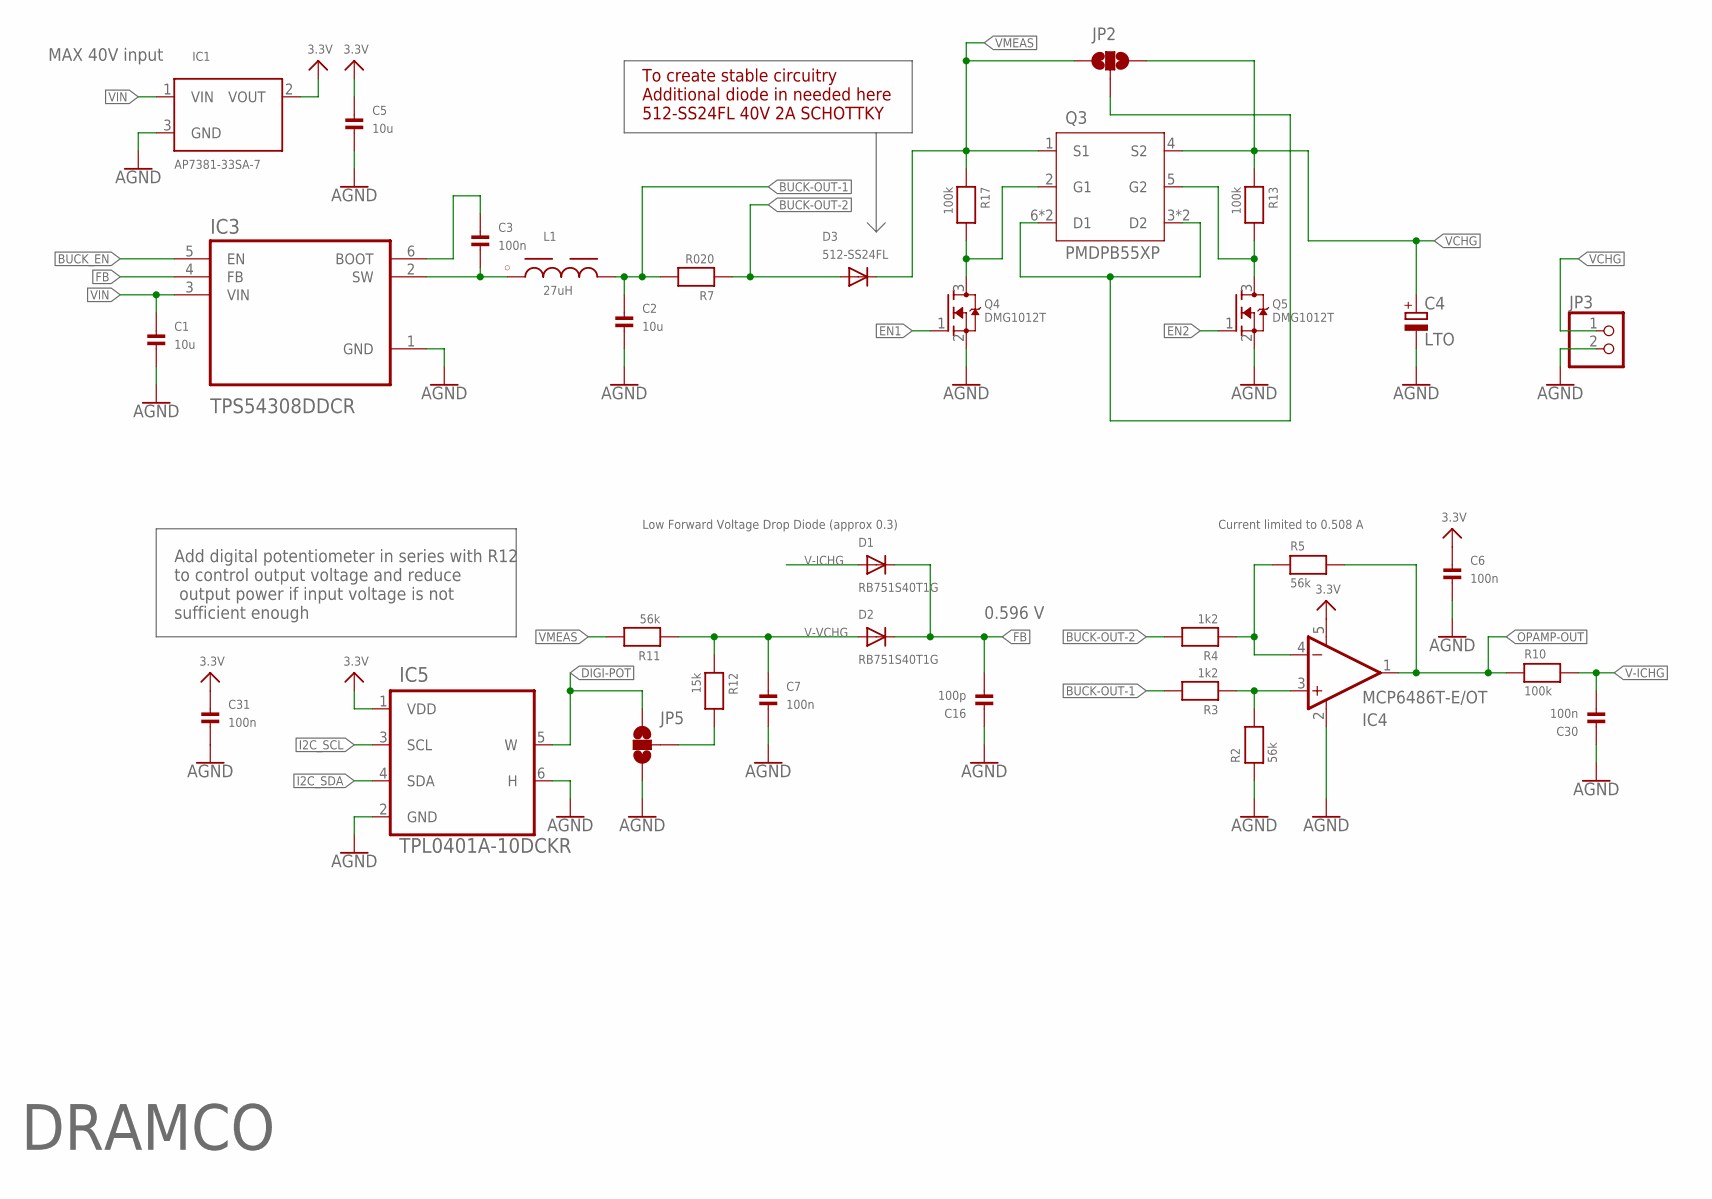
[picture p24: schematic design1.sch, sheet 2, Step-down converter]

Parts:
C1, C2, C5: 10u; 0603
C3, C7, C30: 100n; 0603
C4: LTO; E5-10,5
C6, C31: 100n; 0402
C16: 100p; 0603
D1, D2: RB751S40T1G; SOD-523
D3: 512-SS24FL; SOD-123
IC1: AP7381-33SA-7; SOT23-R
IC3: TPS54308DDCR; SOT95P280X110-6N
IC4: MCP6486T-E/OT; SOT23-5
IC5: TPL0401A-10DCKR; SOT65P210X110-6N
JP2, JP5: JUMPER-SMT_3_NO_NO-SILK; SMT-JUMPER_3_NO_NO-SILK
JP3: HEADER-1X2ROUND; 1X02_ROUND
L1: 27uH; WE-PD_7332/7345_PLASTIC_BASE
Q3: PMDPB55XP; SON65P200X200X65-8N
Q4, Q5: DMG1012T; SOT523-3
R2, R5, R11: 56k; 0603
R3, R4: 1k2; 0603
R7: R020; 0603
R10: 100k; 0603
R12: 15k; 0603
R13, R17: 100k; 0402

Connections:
3.3V: C5.1, C6.1, C31.1, IC1.2 (VOUT), IC4.5 (V+), IC5.1 (VDD)
AGND: C1.2, C2.2, C4.-, C5.2, C6.2, C7.2, C16.1, C30.1, C31.2, IC1.3 (GND), IC3.1 (GND), IC4.2 (V-), IC5.2 (GND), IC5.6 (H), JP3.2, JP5.1, Q4.2 (S), Q5.2 (S), R2.1; also elsewhere on the board
BUCK-OUT-1: C2.1, L1.2, R3.2, R7.2
BUCK-OUT-2: D3.A, R4.2, R7.1
BUCK_EN: IC3.5 (EN); also elsewhere on the board
DIGI-POT: IC5.5 (W), JP5.3
EN1: Q4.1 (G); also elsewhere on the board
EN2: Q5.1 (G); also elsewhere on the board
FB: C16.2, D1.K (C), D2.K (C), IC3.4 (FB)
I2C_SCL: IC5.3 (SCL); also elsewhere on the board
I2C_SDA: IC5.4 (SDA); also elsewhere on the board
unnamed: JP2.2, Q3.3 (D2), Q3.6 (D1), Q3.7 (D1), Q3.8 (D2)
unnamed: C3.1, IC3.6 (BOOT)
unnamed: C3.2, IC3.2 (SW), L1.1
unnamed: JP5.2, R12.2
unnamed: IC4.4 (-IN), R4.1, R5.1
unnamed: IC4.3 (+IN), R2.2, R3.1
unnamed: Q3.2 (G1), Q4.3 (D), R17.2
unnamed: Q3.5 (G2), Q5.3 (D), R13.2
OPAMP-OUT: IC4.1 (OUT), R5.2, R10.1
V-ICHG: C30.2, D1.A, R10.2; also elsewhere on the board
V-VCHG: C7.1, D2.A, R11.1, R12.1
VCHG: C4.+, JP2.3, JP3.1, Q3.4 (S2), R13.1; also elsewhere on the board
VIN: C1.1, IC1.1 (VIN), IC3.3 (VIN); also elsewhere on the board
VMEAS: D3.C, JP2.1, Q3.1 (S1), R11.2, R17.1

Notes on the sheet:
Low Forward Voltage Drop Diode (approx 0.3)
0.596 V
To create stable circuitry Additional diode in needed here 512-SS24FL 40V 2A SCHOTTKY
Add digital potentiometer in series with R12 to control output voltage and reduce output power if input voltage is not sufficient enough
DRAMCO
Current limited to 0.508 A
MAX 40V input

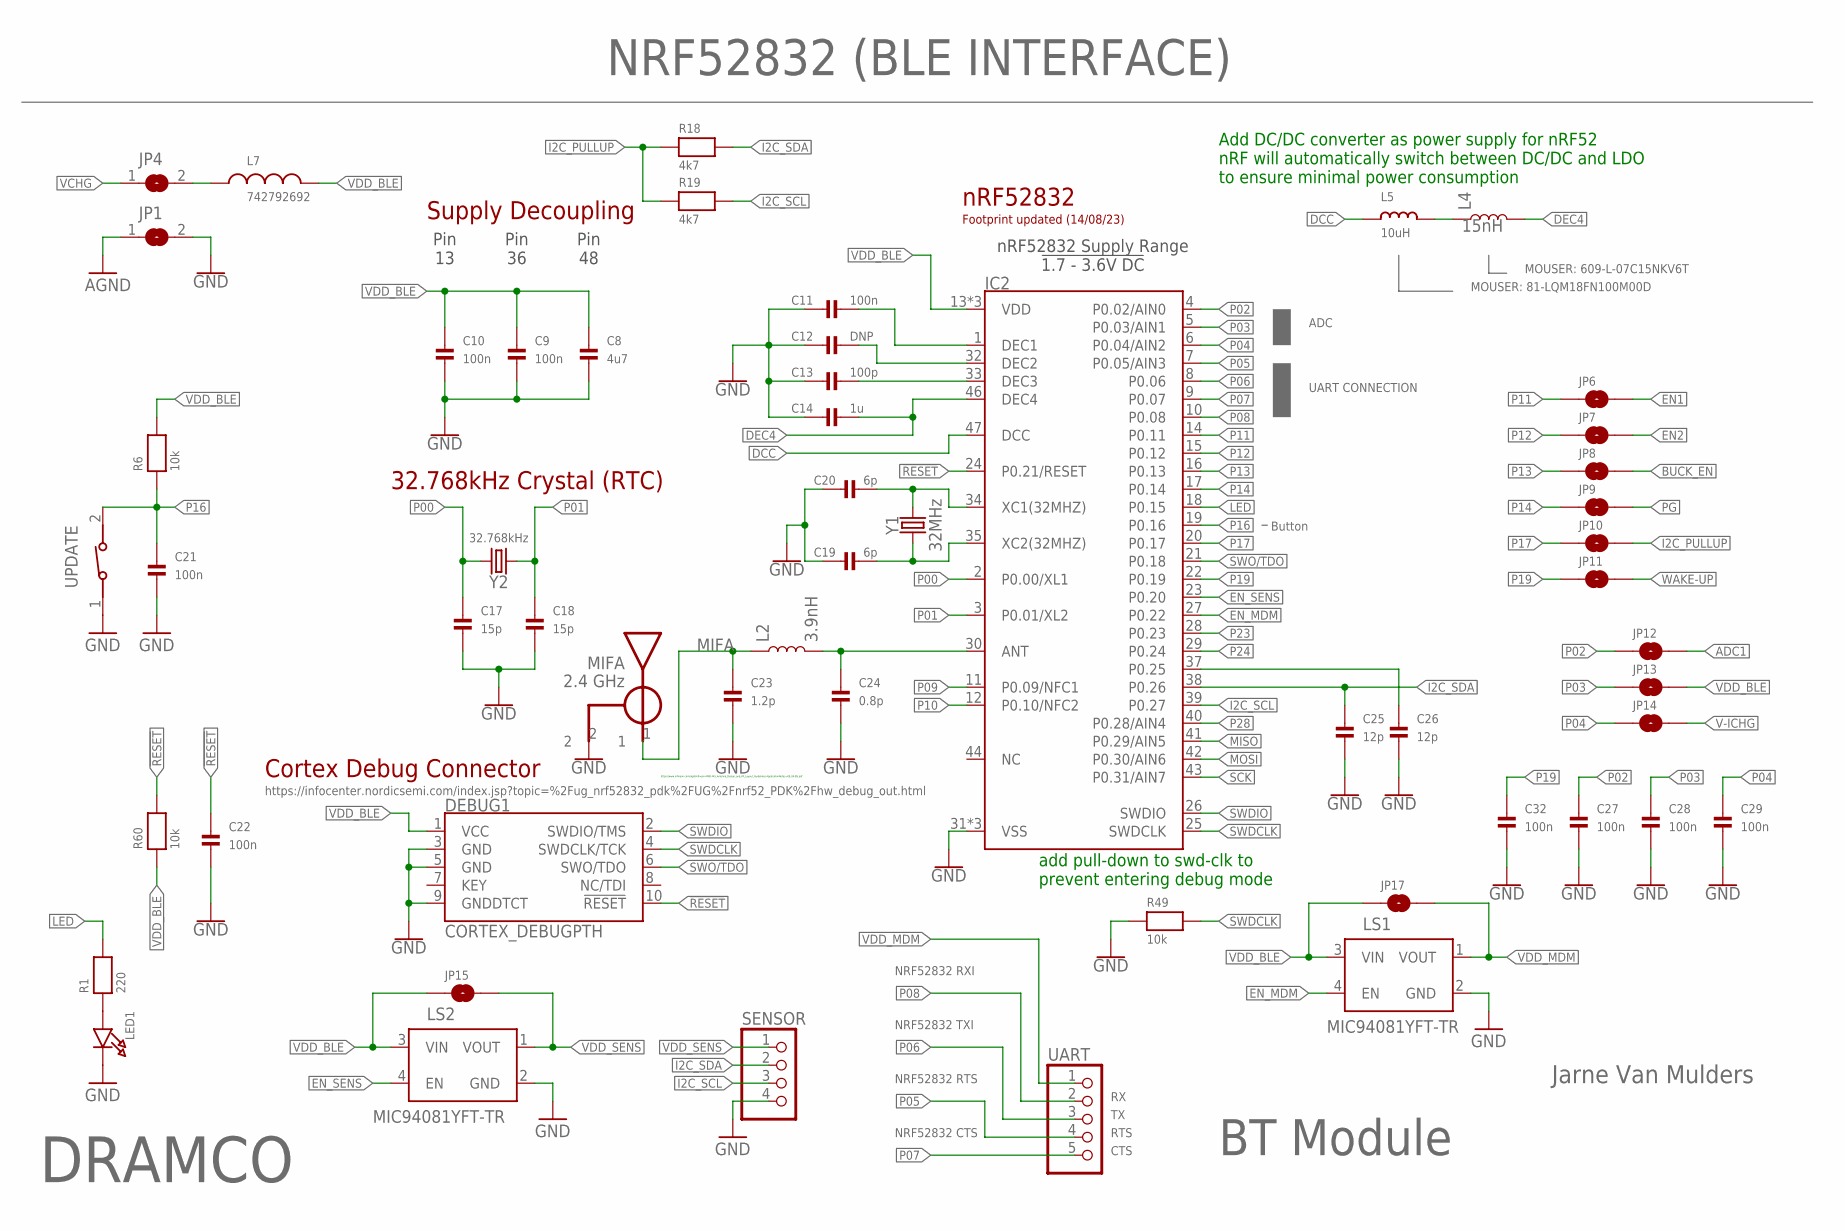
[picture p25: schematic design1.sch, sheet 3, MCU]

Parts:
C8: 4u7; 0603
C9, C10, C11, C21, C22, C27, C28, C29, C32: 100n; 0402
C12: DNP; 0402
C13: 100p; 0402
C14: 1u; 0402
C17, C18: 15p; 0402
C19, C20: 6p; 0402
C23: 1.2p; 0402
C24: 0.8p; 0402
C25, C26: 12p; 0402
DEBUG1: CORTEX_DEBUGPTH; 2X5-PTH-1.27MM
IC2: NRF52832-EXTENDED; QFN48-6X6MM-EXTENDED
JP1, JP4: SOLDERJUMPERREFLOW_NOPASTE; SOLDERJUMPER_REFLOW_NOPASTE
JP6, JP7, JP8, JP9, JP10, JP11, JP12, JP13, JP14, JP15, JP17: JUMPER-SMT_2_NO_NO-SILK; SMT-JUMPER_2_NO_NO-SILK
L2: 3.9nH; 0402
L4: 15nH; 0402
L5: 10uH; _0603MP
L7: 742792692; WE-CBF_0603(W=2.2)
LED1: LED0805; CHIPLED_0805
LS1, LS2: MIC94081YFT-TR; IC_MIC94081YFT-TR
R1: 220; 0603
R6, R49, R60: 10k; 0402
R18, R19: 4k7; 0402
SENSOR: HEADER-1X4ROUND; 1X04_ROUND
U$18: BLE-ANT; ANT-2G4
UART: HEADER-1X5ROUND; 1X05_ROUND
UPDATE: 434111043826
Y1: 32MHz; CRYSTAL-SMD-2.0X1.6MM
Y2: 32.768kHz; CRYSTAL-SMD-3.2X1.5MM

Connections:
!RESET!: C22.1, DEBUG1.10 (!RESET), IC2.24 (P0.21/RESET), R60.2
ADC1: JP12.2; also elsewhere on the board
AGND: JP1.1; also elsewhere on the board
ANT: C24.1, IC2.30 (ANT), L2.2
BUCK_EN: JP8.2; also elsewhere on the board
DCC: IC2.47 (DCC), L5.1
DEC4: C14.2, IC2.46 (DEC4), L4.2
DEC5: C11.2, IC2.1 (DEC1)
DEC6: C12.2, IC2.32 (DEC2)
DEC8: C13.2, IC2.33 (DEC3)
EN1: JP6.2; also elsewhere on the board
EN2: JP7.2; also elsewhere on the board
EN_MDM: IC2.27 (P0.22), LS1.4 (EN)
EN_SENS: IC2.23 (P0.20), LS2.4 (EN)
GND: C8.2, C9.2, C10.2, C11.1, C12.1, C13.1, C14.1, C17.2, C18.2, C19.1, C20.1, C21.2, C22.2, C23.2, C24.2, C25.2, C26.2, C27.2, C28.2, C29.2, C32.2, DEBUG1.3 (GND), DEBUG1.5 (GND), DEBUG1.9 (GNDDTCT), IC2.31 (VSS), IC2.45 (VSS), IC2.EP (VSS), JP1.2, LED1.C, LS1.2 (GND), LS2.2 (GND), R49.1, SENSOR.4, U$18.2, UPDATE.1
I2C_PULLUP: JP10.2, R18.1, R19.1
I2C_SCL: IC2.39 (P0.27), R19.2, SENSOR.3; also elsewhere on the board
I2C_SDA: C25.1, IC2.38 (P0.26), R18.2, SENSOR.2; also elsewhere on the board
LED: IC2.18 (P0.15), R1.2
MIFA: C23.1, L2.1, U$18.1
MISO: IC2.41 (P0.29/AIN5)
MOSI: IC2.42 (P0.30/AIN6)
unnamed: JP4.2, L7.1
unnamed: LED1.A, R1.1
unnamed: C26.1, IC2.37 (P0.25)
unnamed: L4.1, L5.2
P00: C17.1, IC2.2 (P0.00/XL1), Y2.P$2 (2)
P01: C18.1, IC2.3 (P0.01/XL2), Y2.P$1 (1)
P02: C27.1, IC2.4 (P0.02/AIN0), JP12.1
P03: C28.1, IC2.5 (P0.03/AIN1), JP13.1
P04: C29.1, IC2.6 (P0.04/AIN2), JP14.1
P05: IC2.7 (P0.05/AIN3), UART.4
P06: IC2.8 (P0.06), UART.3
P07: IC2.9 (P0.07), UART.5
P08: IC2.10 (P0.08), UART.2
P09: IC2.11 (P0.09/NFC1)
P10: IC2.12 (P0.10/NFC2)
P11: IC2.14 (P0.11), JP6.1
P12: IC2.15 (P0.12), JP7.1
P13: IC2.16 (P0.13), JP8.1
P14: IC2.17 (P0.14), JP9.1
P16: C21.1, IC2.19 (P0.16), R6.1, UPDATE.2
P17: IC2.20 (P0.17), JP10.1
P19: C32.1, IC2.22 (P0.19), JP11.1
P23: IC2.28 (P0.23)
P24: IC2.29 (P0.24)
P28: IC2.40 (P0.28/AIN4)
PG: JP9.2; also elsewhere on the board
SCK: IC2.43 (P0.31/AIN7)
SWDCLK: DEBUG1.4 (SWDCLK/TCK), IC2.25 (SWDCLK), R49.2
SWDIO: DEBUG1.2 (SWDIO/TMS), IC2.26 (SWDIO)
SWO/TDO: DEBUG1.6 (SWO/TDO), IC2.21 (P0.18)
V-ICHG: JP14.2; also elsewhere on the board
VCHG: JP4.1; also elsewhere on the board
VDD_BLE: C8.1, C9.1, C10.1, DEBUG1.1 (VCC), IC2.13 (VDD), IC2.36 (VDD), IC2.48 (VDD), JP13.2, JP15.1, JP17.1, L7.2, LS1.3 (VIN), LS2.3 (VIN), R6.2, R60.1
VDD_MDM: JP17.2, LS1.1 (VOUT), UART.1
VDD_SENS: JP15.2, LS2.1 (VOUT), SENSOR.1
WAKE-UP: JP11.2; also elsewhere on the board
XC1: C20.2, IC2.34 (XC1(32MHZ)), Y1.3 (2)
XC2: C19.2, IC2.35 (XC2(32MHZ)), Y1.1

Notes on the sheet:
BT Module
Jarne Van Mulders
DRAMCO
NRF52832 (BLE INTERFACE)
Pin 13
Pin 36
Pin 48
nRF52832
32.768kHz Crystal (RTC)
Supply Decoupling
Cortex Debug Connector
nRF52832 Supply Range !1.7 - 3.6V DC!
Add DC/DC converter as power supply for nRF52 nRF will automatically switch between DC/DC and LDO to ensure minimal power consumption
add pull-down to swd-clk to prevent entering debug mode
NRF52832 RXI
NRF52832 TXI
NRF52832 RTS
NRF52832 CTS
MOUSER: 81-LQM18FN100M00D
MOUSER: 609-L-07C15NKV6T
RTS
CTS
UART CONNECTION
Button
ADC
https://www.infineon.com/dgdl/Infineon-AN91445_Antenna_Design_and_RF_Layout_Guidelines-ApplicationNotes-v09_00-EN.pdf
https://infocenter.nordicsemi.com/index.jsp?topic=%2Fug_nrf52832_pdk%2FUG%2Fnrf52_PDK%2Fhw_debug_out.html
Footprint updated (14/08/23)

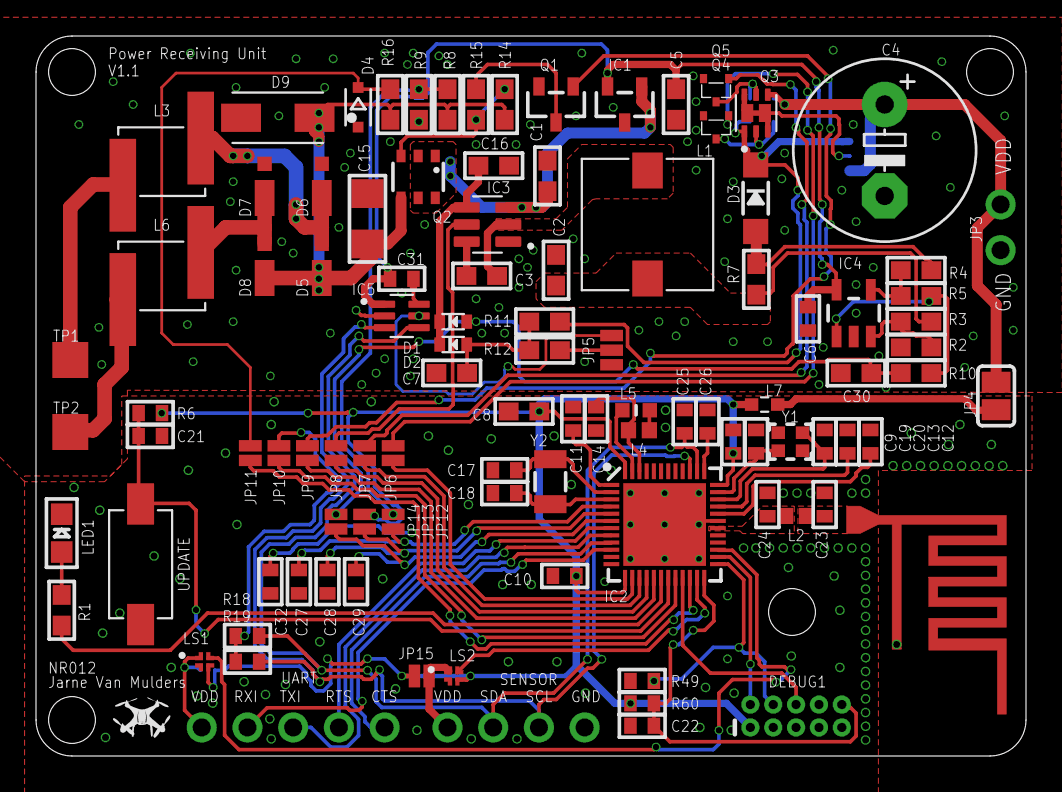
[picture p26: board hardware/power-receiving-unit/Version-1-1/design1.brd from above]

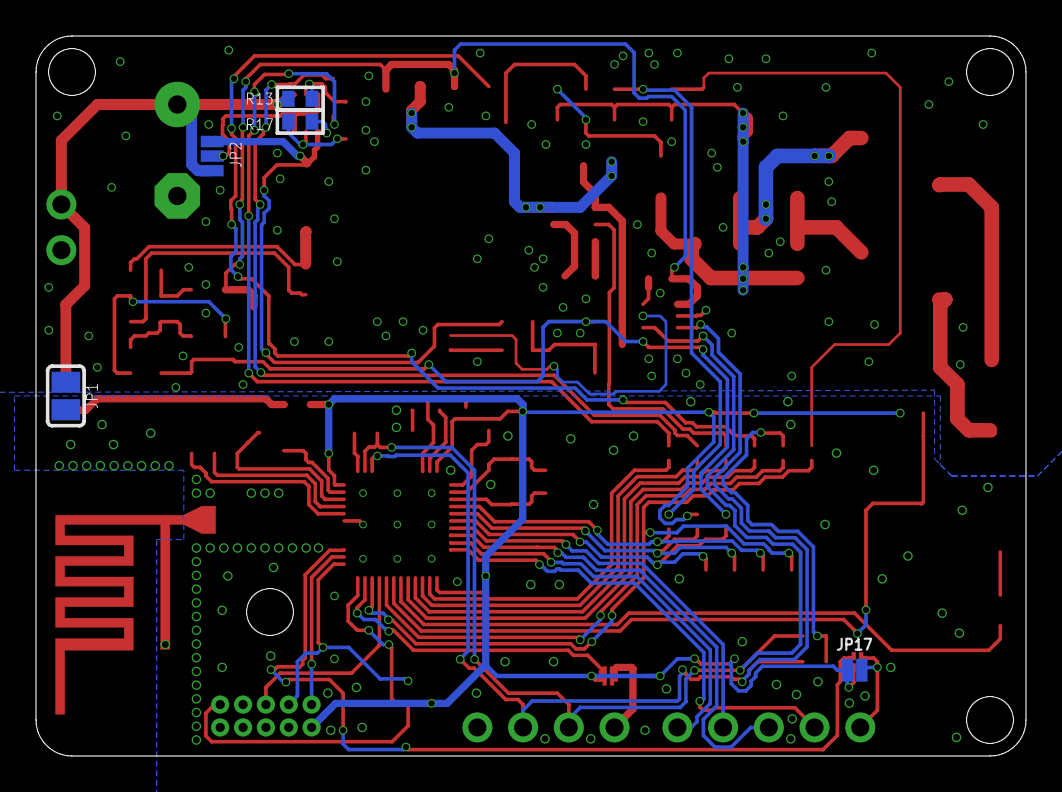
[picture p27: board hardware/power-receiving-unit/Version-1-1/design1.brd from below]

Board: 2 copper layers, 55.0 x 40.0 mm, 107 parts (5 on the bottom side), 76 nets.

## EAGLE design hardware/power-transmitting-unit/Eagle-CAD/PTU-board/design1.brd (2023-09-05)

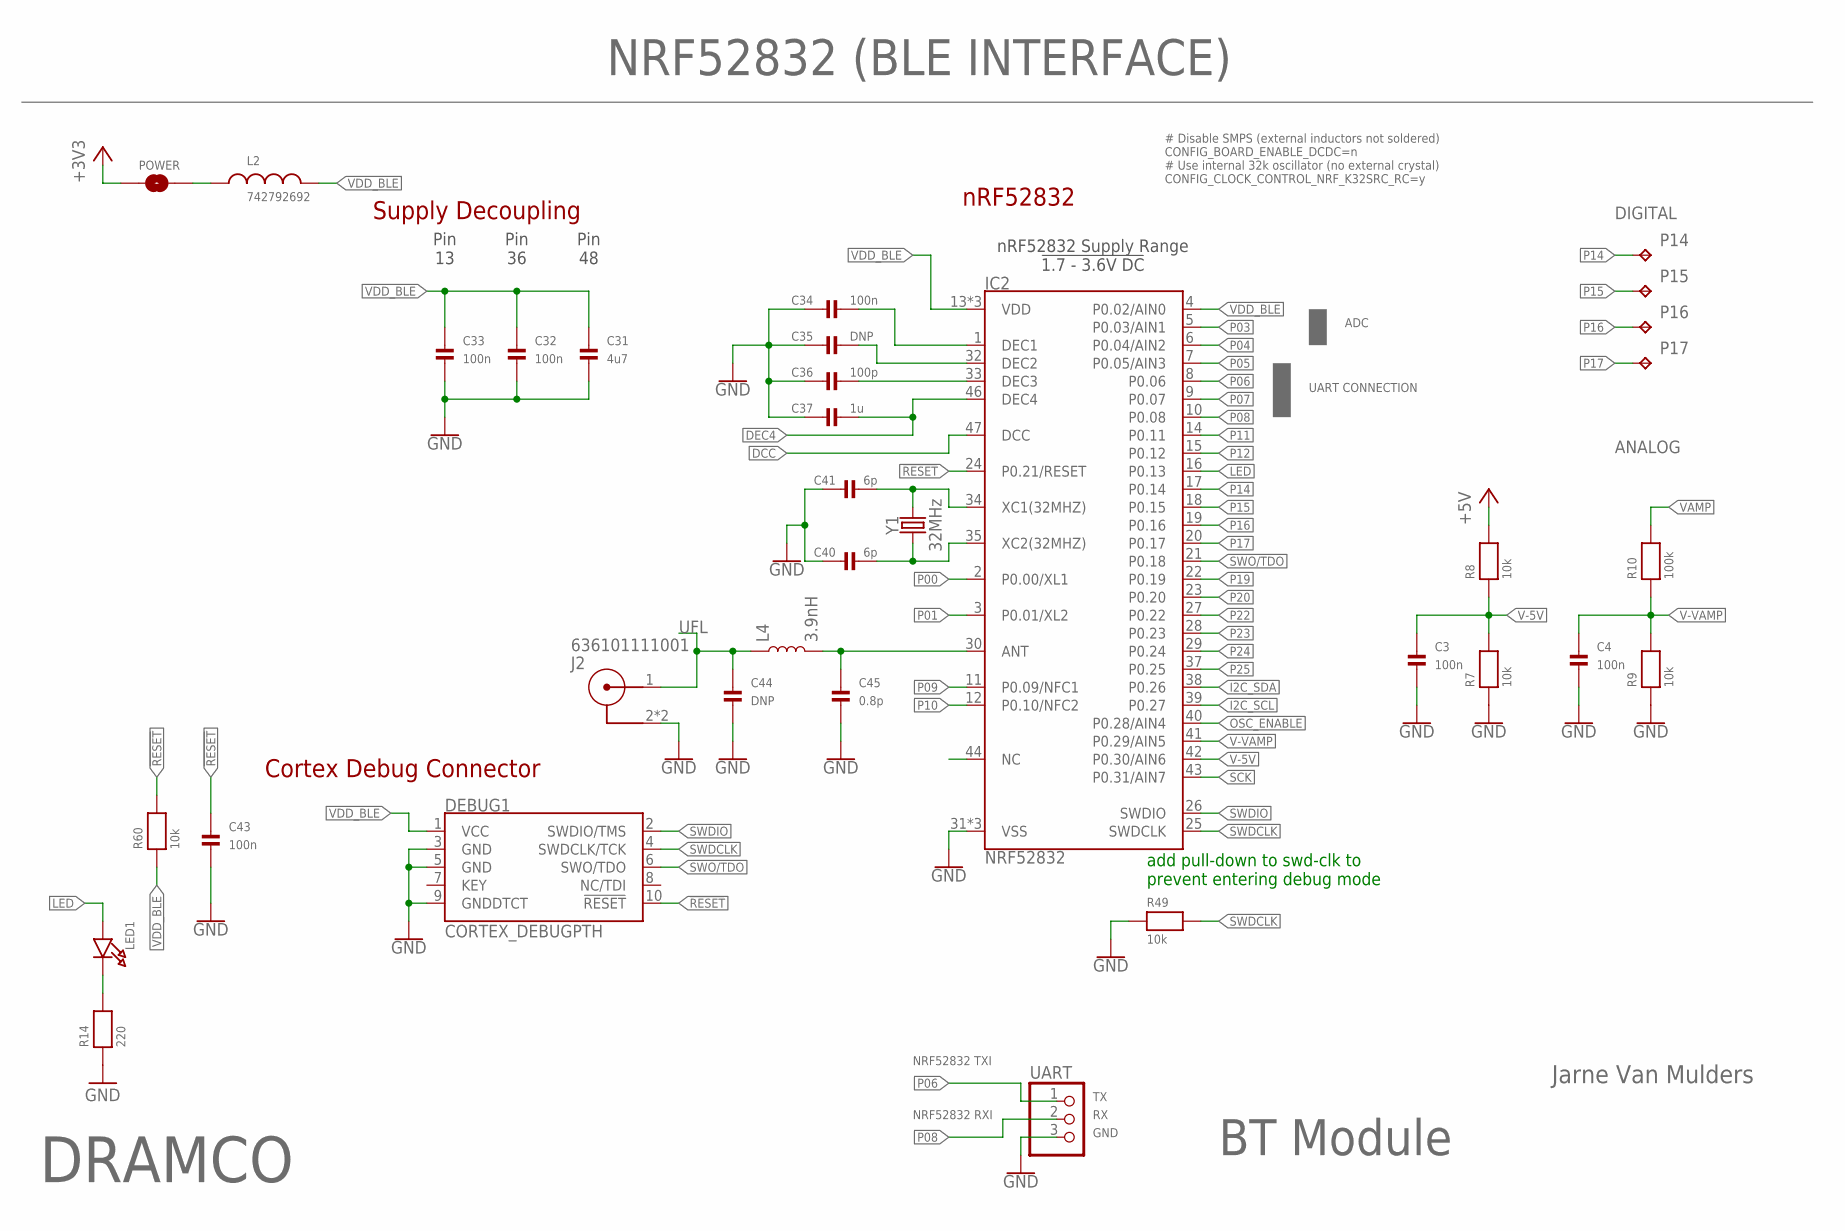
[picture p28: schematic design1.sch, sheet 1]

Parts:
C3, C4, C32, C33, C34, C43: 100n; 0402
C31: 4u7; 0603
C35, C44: DNP; 0402
C36: 100p; 0402
C37: 1u; 0402
C40, C41: 6p; 0402
C45: 0.8p; 0402
DEBUG1: CORTEX_DEBUGPTH; 2X5-PTH-1.27MM
IC2: NRF52832; QFN48-6X6MM-EXTENDED
J2: 636101111001
L2: 742792692; WE-CBF_0603(W=2.2)
L4: 3.9nH; 0402
LED1: LED0805; CHIPLED_0805
P14, P15, P16, P17: TPTP10SQ; TP10SQ
POWER: JUMPER-SMT_2_NO_NO-SILK; SMT-JUMPER_2_NO_NO-SILK
R7, R8, R9, R49, R60: 10k; 0402
R10: 100k; 0402
R14: 220; 0603
UART: HEADER-1X3ROUND; 1X03_ROUND
Y1: 32MHz; CRYSTAL-SMD-2.0X1.6MM

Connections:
!RESET!: C43.1, DEBUG1.10 (!RESET), IC2.24 (P0.21/RESET), R60.2
+3V3: POWER.1; also elsewhere on the board
+5V: R8.2; also elsewhere on the board
ANT: C45.1, IC2.30 (ANT), L4.2
DCC: IC2.47 (DCC)
DEC4: C37.2, IC2.46 (DEC4)
DEC5: C34.2, IC2.1 (DEC1)
DEC6: C35.2, IC2.32 (DEC2)
DEC8: C36.2, IC2.33 (DEC3)
GND: C3.2, C4.2, C31.2, C32.2, C33.2, C34.1, C35.1, C36.1, C37.1, C40.1, C41.1, C43.2, C44.2, C45.2, DEBUG1.3 (GND), DEBUG1.5 (GND), DEBUG1.9 (GNDDTCT), IC2.31 (VSS), IC2.45 (VSS), IC2.EP (VSS), J2.2, J2.3 (2), R7.1, R9.1, R14.1, R49.1, UART.3; also elsewhere on the board
I2C_SCL: IC2.39 (P0.27); also elsewhere on the board
I2C_SDA: IC2.38 (P0.26); also elsewhere on the board
LED: IC2.16 (P0.13), LED1.A
unnamed: LED1.C, R14.2
unnamed: L2.1, POWER.2
NC: IC2.44 (NC)
OSC_ENABLE: IC2.40 (P0.28/AIN4); also elsewhere on the board
P00: IC2.2 (P0.00/XL1)
P01: IC2.3 (P0.01/XL2)
P03: IC2.5 (P0.03/AIN1)
P04: IC2.6 (P0.04/AIN2)
P05: IC2.7 (P0.05/AIN3)
P06: IC2.8 (P0.06), UART.1
P07: IC2.9 (P0.07)
P08: IC2.10 (P0.08), UART.2
P09: IC2.11 (P0.09/NFC1)
P10: IC2.12 (P0.10/NFC2)
P11: IC2.14 (P0.11)
P12: IC2.15 (P0.12)
P14: IC2.17 (P0.14), P14.TP
P15: IC2.18 (P0.15), P15.TP
P16: IC2.19 (P0.16), P16.TP
P17: IC2.20 (P0.17), P17.TP
P19: IC2.22 (P0.19)
P20: IC2.23 (P0.20)
P22: IC2.27 (P0.22)
P23: IC2.28 (P0.23)
P24: IC2.29 (P0.24)
P25: IC2.37 (P0.25)
SCK: IC2.43 (P0.31/AIN7)
SWDCLK: DEBUG1.4 (SWDCLK/TCK), IC2.25 (SWDCLK), R49.2
SWDIO: DEBUG1.2 (SWDIO/TMS), IC2.26 (SWDIO)
SWO/TDO: DEBUG1.6 (SWO/TDO), IC2.21 (P0.18)
UFL: C44.1, J2.1, L4.1
V-5V: C3.1, IC2.42 (P0.30/AIN6), R7.2, R8.1
V-VAMP: C4.1, IC2.41 (P0.29/AIN5), R9.2, R10.1
VAMP: R10.2; also elsewhere on the board
VDD_BLE: C31.1, C32.1, C33.1, DEBUG1.1 (VCC), IC2.4 (P0.02/AIN0), IC2.13 (VDD), IC2.36 (VDD), IC2.48 (VDD), L2.2, R60.1
XC1: C41.2, IC2.34 (XC1(32MHZ)), Y1.3 (2)
XC2: C40.2, IC2.35 (XC2(32MHZ)), Y1.1

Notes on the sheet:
BT Module
Jarne Van Mulders
DRAMCO
NRF52832 (BLE INTERFACE)
Pin 13
Pin 36
Pin 48
nRF52832
Supply Decoupling
Cortex Debug Connector
nRF52832 Supply Range !1.7 - 3.6V DC!
add pull-down to swd-clk to prevent entering debug mode
NRF52832 RXI
NRF52832 TXI
UART CONNECTION
ADC
ANALOG
DIGITAL
# Disable SMPS (external inductors not soldered) CONFIG_BOARD_ENABLE_DCDC=n # Use internal 32k oscillator (no external crystal) CONFIG_CLOCK_CONTROL_NRF_K32SRC_RC=y
GND

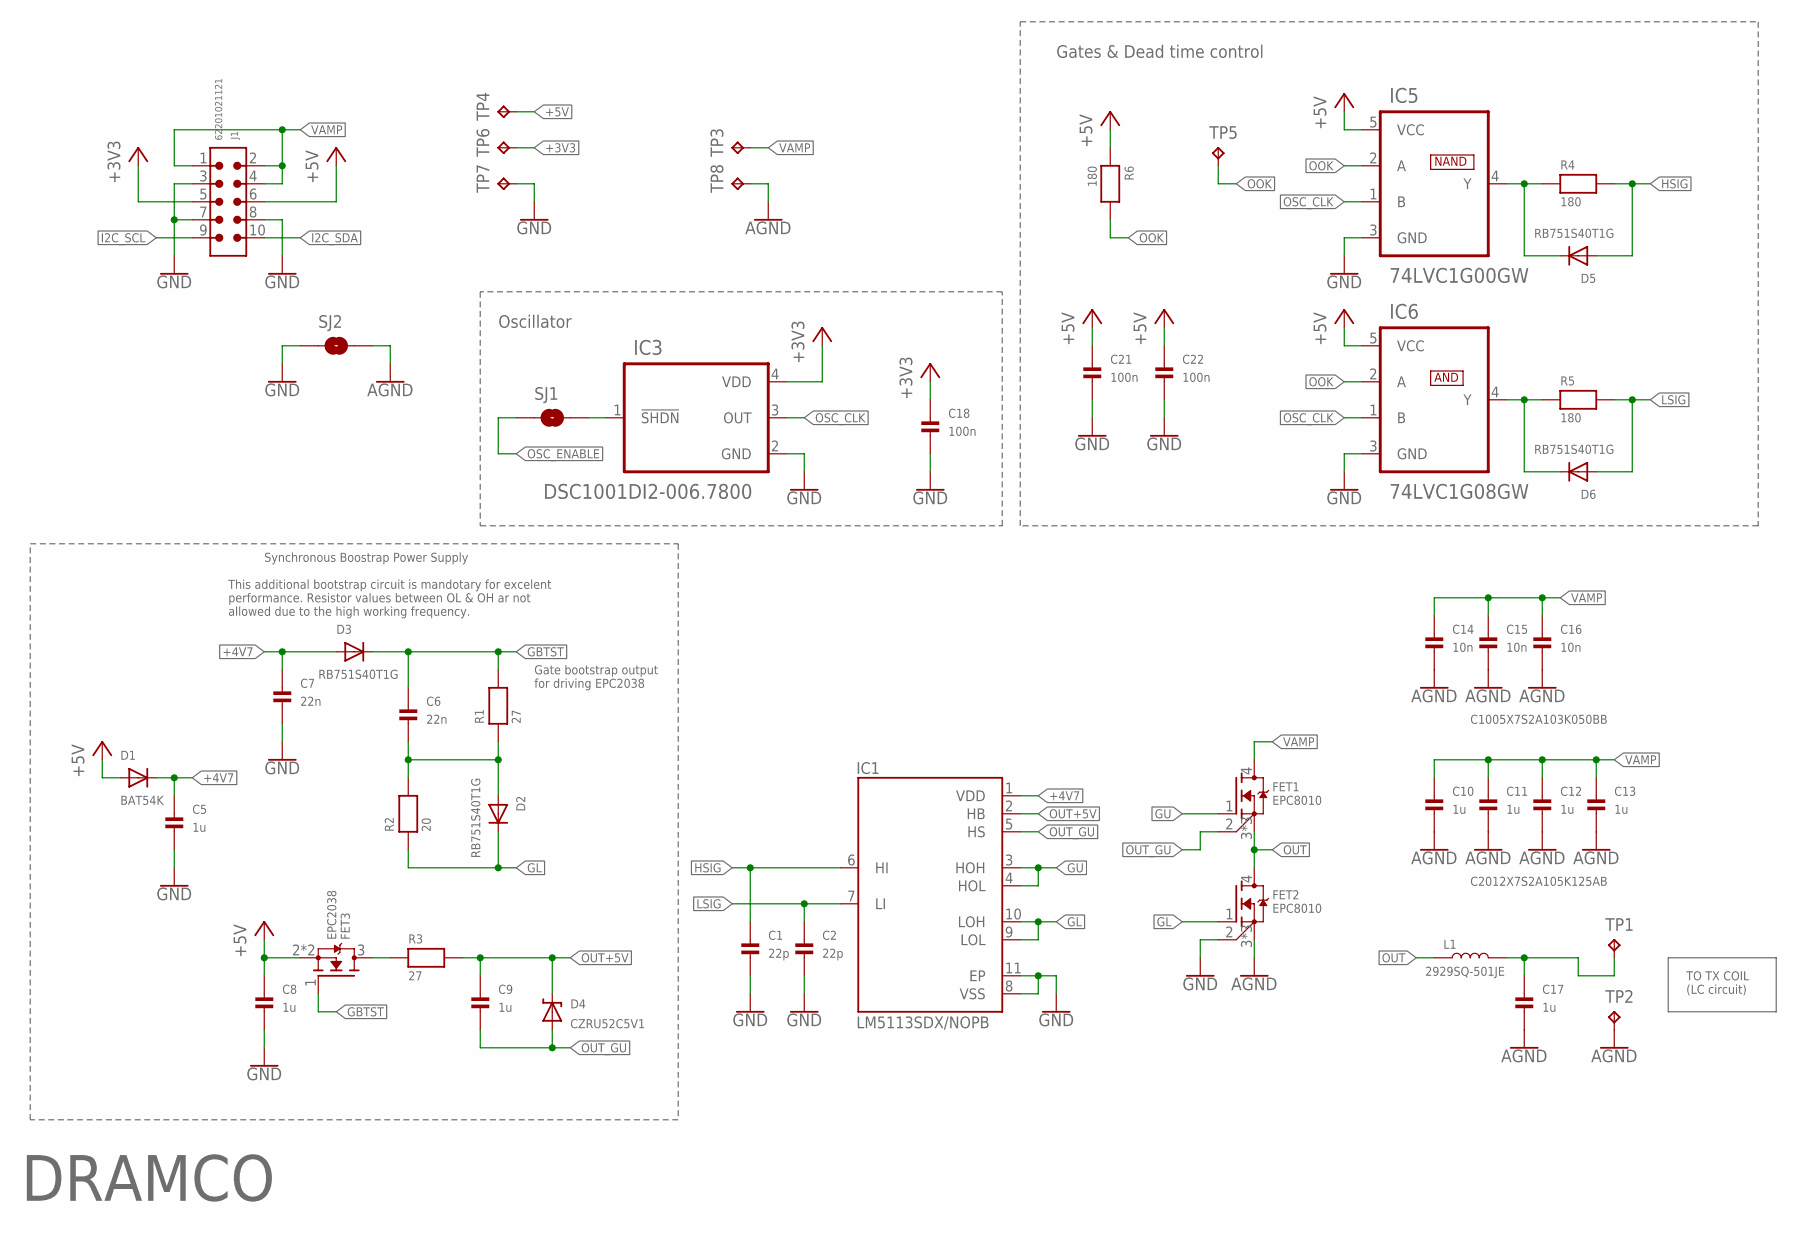
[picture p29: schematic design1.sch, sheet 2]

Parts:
C1, C2: 22p; 0402
C5, C8, C9: 1u; 0402
C6, C7: 22n; 0402
C10, C11, C12, C13, C17: 1u; 0805
C14, C15, C16: 10n; 0402
C18: 100n; 0603
C21, C22: 100n; 0402
D1: BAT54K; SOD-523
D2, D3, D5, D6: RB751S40T1G; SOD-523
D4: CZRU52C5V1; SOD-523F
FET1, FET2: EPC8010; BGA-8010
FET3: EPC2038; BGA-2038
IC1: LM5113SDX/NOPB; SON80P400X400X80-11N
IC3: DSC1001DI2-006.7800; 2.5X2.0MMPLASTICPACKAGE
IC5: 74LVC1G00GW; SOT65P210X110-5N
IC6: 74LVC1G08GW; SOT65P210X110-5N
J1: 62201021121
L1: 2929SQ-501JE; 2929SQ-501
R1, R3: 27; 0402
R2: 20; 0402
R4, R5, R6: 180; 0402
SJ1, SJ2: SOLDERJUMPERNO; SJ_2S-NO
TP1, TP2, TP3, TP8: TPTP20SQ; TP20SQ
TP4, TP5, TP6, TP7: TPTP10SQ; TP10SQ

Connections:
+3V3: C18.1, IC3.4 (VDD), J1.5, TP6.TP; also elsewhere on the board
+4V7: C5.1, C7.1, D1.K (C), D3.A, IC1.1 (VDD)
+5V: C8.1, C21.1, C22.1, D1.A, FET3.2 (S), FET3.4 (S), IC5.5 (VCC), IC6.5 (VCC), J1.6, R6.1, TP4.TP; also elsewhere on the board
AGND: C10.2, C11.2, C12.2, C13.2, C14.2, C15.2, C16.2, C17.2, FET2.3 (S), FET2.5 (S), FET2.6 (S), SJ2.2, TP2.TP, TP8.TP
GBTST: C6.1, D3.K (C), FET3.1 (G), R1.2
GL: D2.K (C), FET2.1 (G), IC1.9 (LOL), IC1.10 (LOH), R2.1
GND: C1.2, C2.2, C5.2, C7.2, C8.2, C18.2, C21.2, C22.2, FET2.2 (SR), IC1.8 (VSS), IC1.11 (EP), IC3.2 (GND), IC5.3 (GND), IC6.3 (GND), J1.3, J1.7, J1.8, SJ2.1, TP7.TP; also elsewhere on the board
GU: FET1.1 (G), IC1.3 (HOH), IC1.4 (HOL)
HSIG: C1.1, D5.A, IC1.6 (HI), R4.2
I2C_SCL: J1.9; also elsewhere on the board
I2C_SDA: J1.10; also elsewhere on the board
LSIG: C2.1, D6.A, IC1.7 (LI), R5.2
unnamed: FET3.3 (D), R3.1
unnamed: D5.K (C), IC5.4 (Y), R4.1
unnamed: IC3.1 (!SHDN!), SJ1.2
unnamed: D6.K (C), IC6.4 (Y), R5.1
unnamed: C6.2, D2.A, R1.1, R2.2
unnamed: C17.1, L1.2, TP1.TP
OOK: IC5.2 (A), IC6.2 (A), R6.2, TP5.TP
OSC_CLK: IC3.3 (OUT), IC5.1 (B), IC6.1 (B)
OSC_ENABLE: SJ1.1; also elsewhere on the board
OUT: FET1.3 (S), FET1.5 (S), FET1.6 (S), FET2.4 (D), L1.1
OUT+5V: C9.1, D4.1 (C), IC1.2 (HB), R3.2
OUT_GU: C9.2, D4.2 (A), FET1.2 (SR), IC1.5 (HS)
VAMP: C10.1, C11.1, C12.1, C13.1, C14.1, C15.1, C16.1, FET1.4 (D), J1.1, J1.2, J1.4, TP3.TP; also elsewhere on the board

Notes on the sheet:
Synchronous Boostrap Power Supply
This additional bootstrap circuit is mandotary for excelent performance. Resistor values between OL & OH ar not allowed due to the high working frequency.
Gate bootstrap output for driving EPC2038
C2012X7S2A105K125AB
C1005X7S2A103K050BB
TO TX COIL (LC circuit)
NAND
AND
Gates & Dead time control
Oscillator
DRAMCO

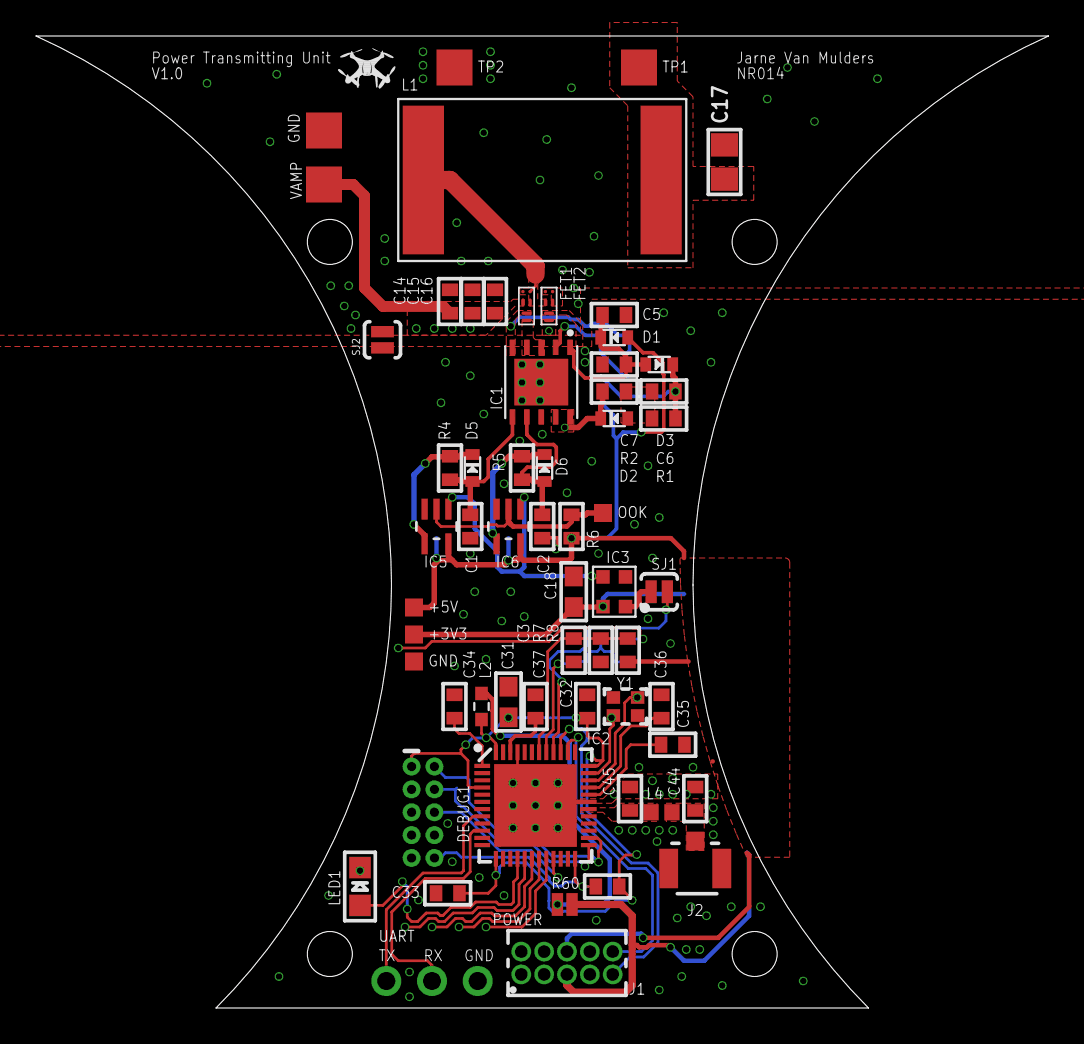
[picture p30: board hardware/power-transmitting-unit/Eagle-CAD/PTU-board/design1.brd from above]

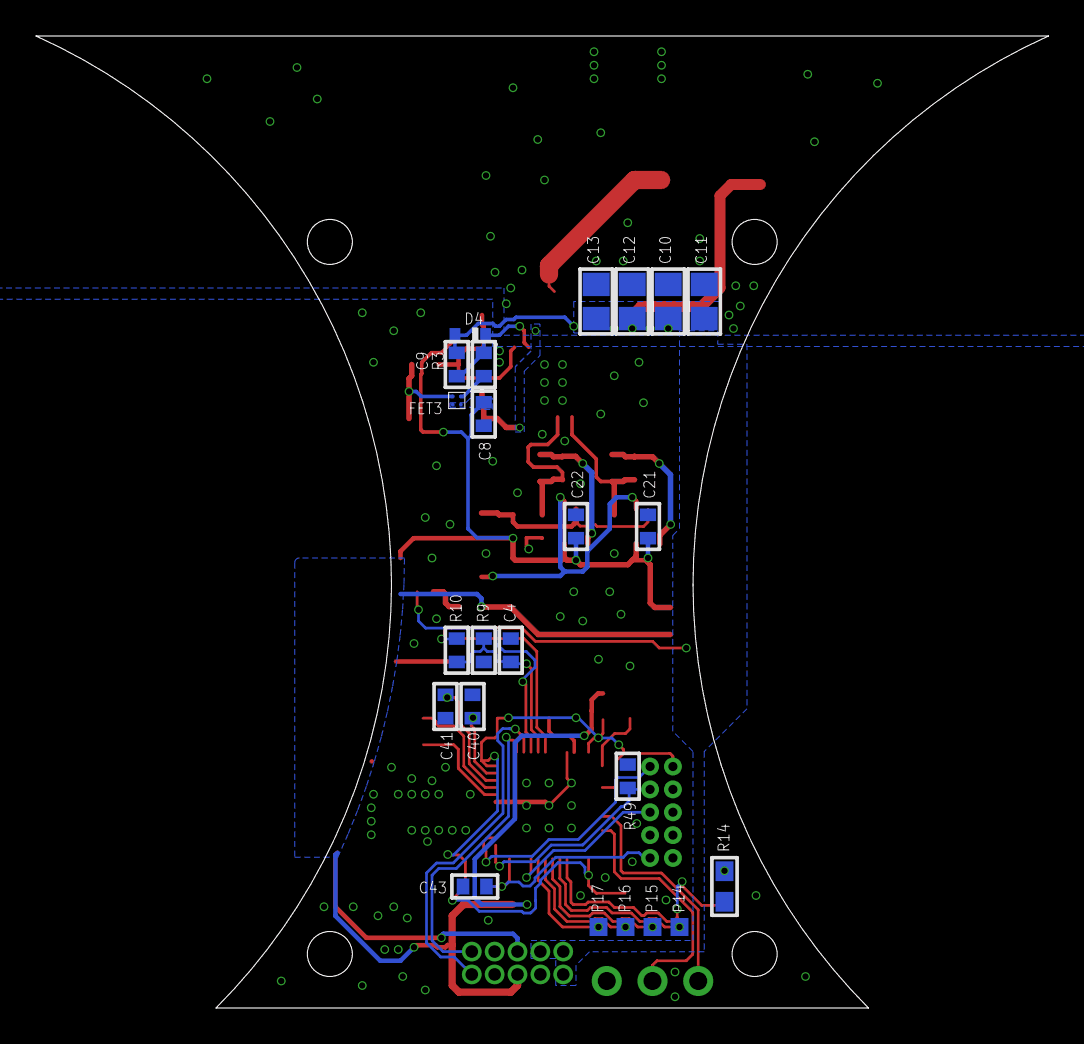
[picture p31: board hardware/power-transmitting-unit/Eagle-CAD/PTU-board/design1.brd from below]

Board: 2 copper layers, 56.2 x 54.0 mm, 83 parts (23 on the bottom side), 49 nets.

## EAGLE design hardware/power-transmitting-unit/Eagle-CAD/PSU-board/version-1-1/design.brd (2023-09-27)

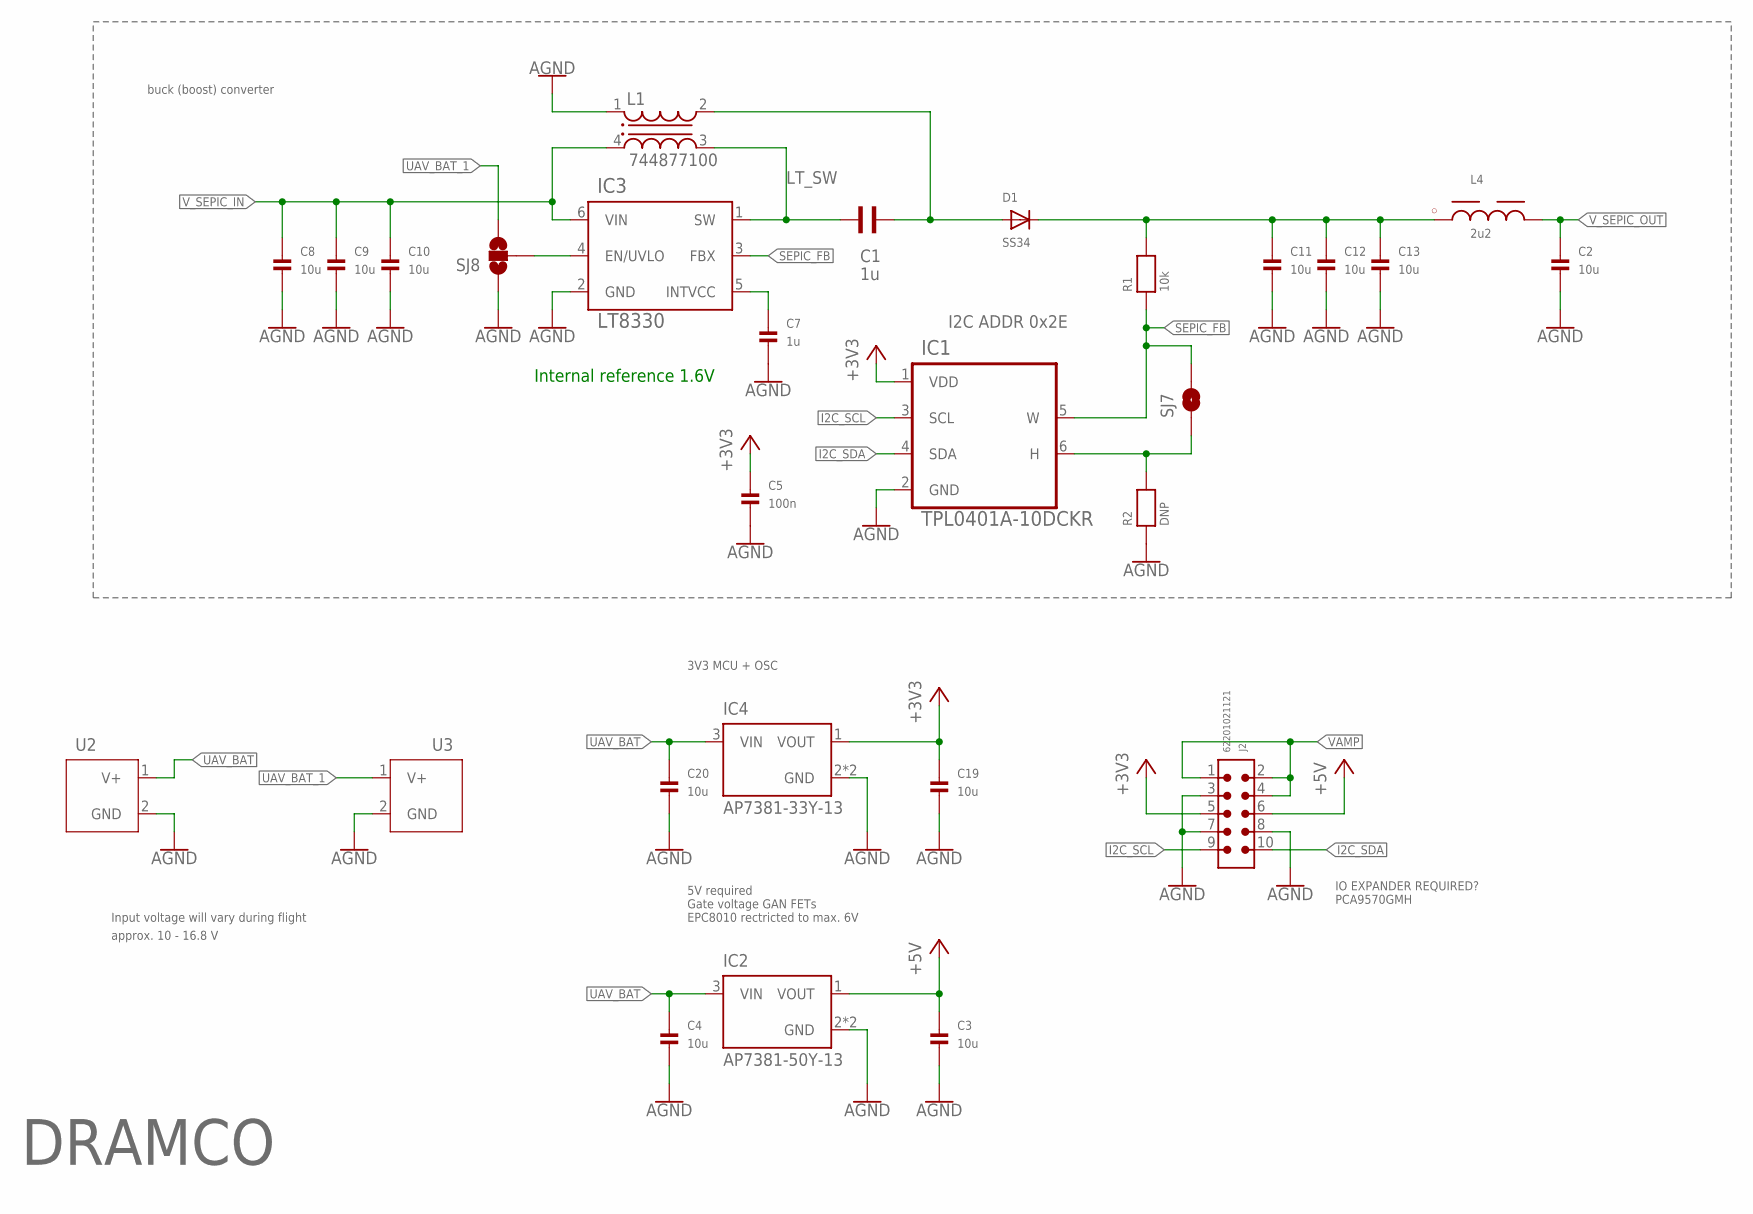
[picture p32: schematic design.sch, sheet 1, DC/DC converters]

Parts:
C1: 1u; WCAP-CSGP_0805_WAVE
C2: 10u; 0805
C3, C4, C19, C20: 10u; 0603
C5: 100n; 0402
C7: 1u; 0603
C8, C9, C10, C11, C12, C13: 10u; 1206
D1: SS34; SOD-123
IC1: TPL0401A-10DCKR; SOT65P210X110-6N
IC2: AP7381-50Y-13; FOOT_XC6201P332PR-G
IC3: LT8330; TSOT-23_S6
IC4: AP7381-33Y-13; FOOT_XC6201P332PR-G
J2: 62201021121
L1: 744877100; WE-DD_7345
L4: 2u2; WE-LQS_3015
R1: 10k; 0603
R2: DNP; 0603
SJ7: SOLDERJUMPERNO; SJ_2S-NO
SJ8: SOLDERJUMPER_2WAYS; SJ_3
U2, U3: UAV-CONNECT; HOLE

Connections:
+3V3: C5.1, C19.1, IC1.1 (VDD), IC4.1 (VOUT), J2.5; also elsewhere on the board
+5V: C3.1, IC2.1 (VOUT), J2.6; also elsewhere on the board
AGND: C2.2, C3.2, C4.2, C5.2, C7.2, C8.2, C9.2, C10.2, C11.2, C12.2, C13.2, C19.2, C20.2, IC1.2 (GND), IC2.2 (GND), IC2.2.1 (GND), IC3.2 (GND), IC4.2 (GND), IC4.2.1 (GND), J2.3, J2.7, J2.8, L1.1, R2.1, SJ8.1, U2.2 (GND), U3.2 (GND); also elsewhere on the board
I2C_SCL: IC1.3 (SCL), J2.9; also elsewhere on the board
I2C_SDA: IC1.4 (SDA), J2.10; also elsewhere on the board
LT_SW: C1.2, IC3.1 (SW), L1.3
unnamed: C7.1, IC3.5 (INTVCC)
unnamed: C1.1, D1.A, L1.2
unnamed: C11.1, C12.1, C13.1, D1.C, L4.1, R1.2
unnamed: IC3.4 (EN/UVLO), SJ8.2
unnamed: IC1.6 (H), R2.2, SJ7.1
SEPIC_FB: IC1.5 (W), IC3.3 (FBX), R1.1, SJ7.2
UAV_BAT: C4.1, C20.1, IC2.3 (VIN), IC4.3 (VIN), U2.1 (V+); also elsewhere on the board
UAV_BAT_1: SJ8.3, U3.1 (V+); also elsewhere on the board
VAMP: J2.1, J2.2, J2.4; also elsewhere on the board
V_SEPIC_IN: C8.1, C9.1, C10.1, IC3.6 (VIN), L1.4; also elsewhere on the board
V_SEPIC_OUT: C2.1, L4.2; also elsewhere on the board

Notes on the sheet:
5V required Gate voltage GAN FETs EPC8010 rectricted to max. 6V
buck (boost) converter
Input voltage will vary during flight
approx. 10 - 16.8 V
3V3 MCU + OSC
IO EXPANDER REQUIRED? PCA9570GMH
DRAMCO
I2C ADDR 0x2E
Internal reference 1.6V

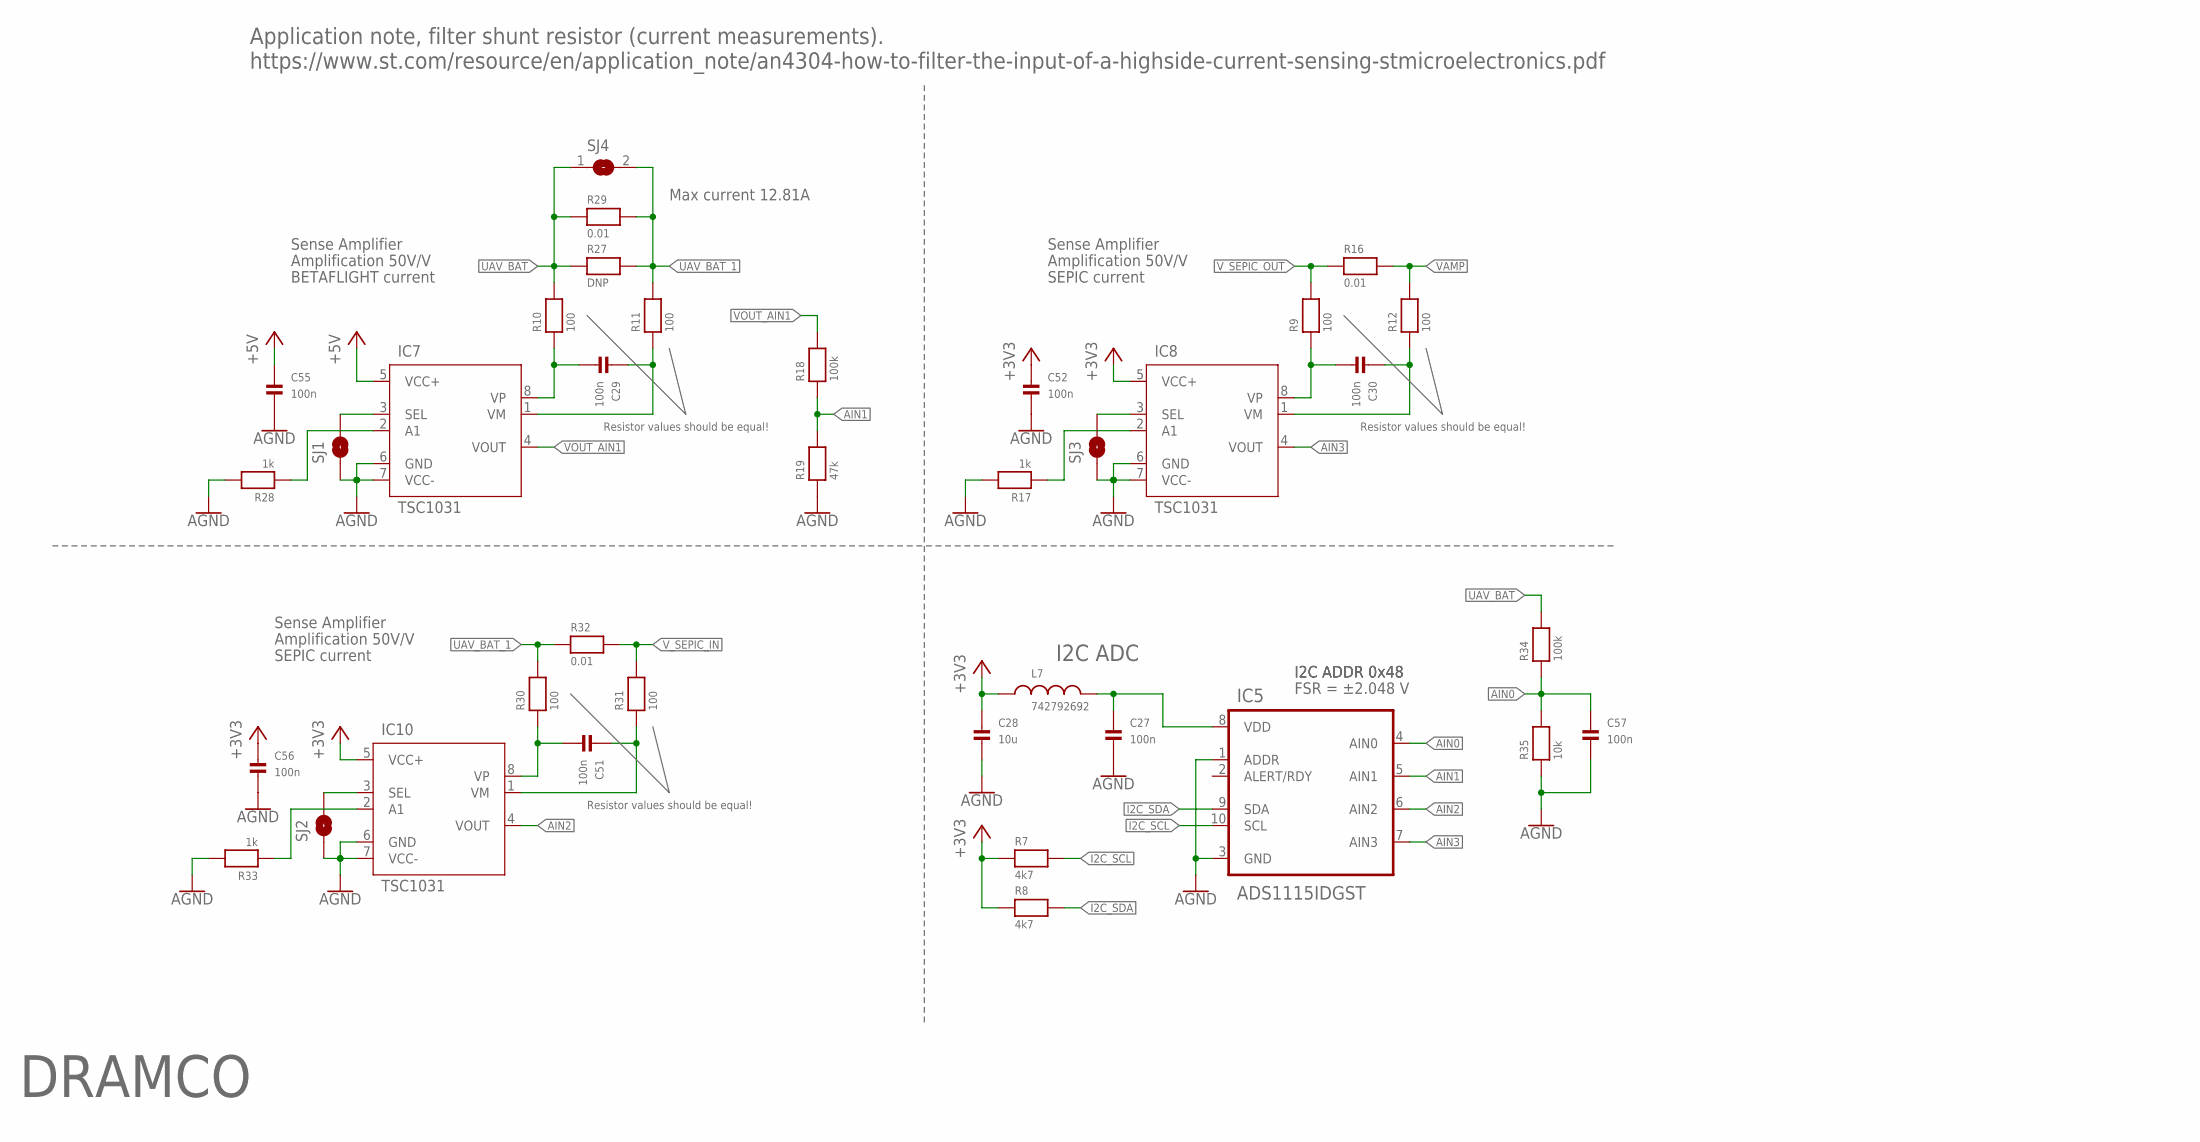
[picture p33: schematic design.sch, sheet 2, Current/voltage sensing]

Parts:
C27, C29, C30, C51, C52, C55, C56, C57: 100n; 0402
C28: 10u; 0603
IC5: ADS1115IDGST; SOP50P490X110-10N
IC7, IC8, IC10: TSC1031; SOP65P640X120-8N
L7: 742792692; WE-CBF_0603(W=2.2)
R7, R8: 4k7; 0603
R9, R10, R11, R12, R30, R31: 100; 0402
R16, R29, R32: 0.01; 0805
R17, R28, R33: 1k; 0402
R18, R34: 100k; 0603
R19: 47k; 0603
R27: DNP; 0805
R35: 10k; 0603
SJ1, SJ2, SJ3: SOLDERJUMPERTRACE; SJ_2S-TRACE
SJ4: SOLDERJUMPERREFLOW; SOLDERJUMPER_REFLOW

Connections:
+3V3: C28.1, C52.1, C56.1, IC8.5 (VCC+), IC10.5 (VCC+), L7.1, R7.1, R8.1; also elsewhere on the board
+5V: C55.1, IC7.5 (VCC+); also elsewhere on the board
AGND: C27.2, C28.2, C52.2, C55.2, C56.2, C57.2, IC5.1 (ADDR), IC5.3 (GND), IC7.6 (GND), IC7.7 (VCC-), IC8.6 (GND), IC8.7 (VCC-), IC10.6 (GND), IC10.7 (VCC-), R17.2, R19.1, R28.2, R33.2, R35.1, SJ1.1, SJ2.1, SJ3.1; also elsewhere on the board
AIN0: C57.1, IC5.4 (AIN0), R34.1, R35.2
AIN1: IC5.5 (AIN1), R18.1, R19.2
AIN2: IC5.6 (AIN2), IC10.4 (VOUT)
AIN3: IC5.7 (AIN3), IC8.4 (VOUT)
I2C_SCL: IC5.10 (SCL), R7.2; also elsewhere on the board
I2C_SDA: IC5.9 (SDA), R8.2; also elsewhere on the board
unnamed: C30.1, IC8.1 (VM), R12.1
unnamed: C27.1, IC5.8 (VDD), L7.2
unnamed: C30.2, IC8.8 (VP), R9.1
unnamed: IC8.3 (SEL), SJ3.2
unnamed: IC8.2 (A1), R17.1
unnamed: IC7.3 (SEL), SJ1.2
unnamed: C29.1, IC7.1 (VM), R11.1
unnamed: C29.2, IC7.8 (VP), R10.1
unnamed: C51.1, IC10.1 (VM), R31.1
unnamed: C51.2, IC10.8 (VP), R30.1
unnamed: IC7.2 (A1), R28.1
unnamed: IC10.3 (SEL), SJ2.2
unnamed: IC10.2 (A1), R33.1
UAV_BAT: R10.2, R27.1, R29.1, R34.2, SJ4.1; also elsewhere on the board
UAV_BAT_1: R11.2, R27.2, R29.2, R30.2, R32.1, SJ4.2; also elsewhere on the board
VAMP: R12.2, R16.2; also elsewhere on the board
VOUT_AIN1: IC7.4 (VOUT), R18.2
V_SEPIC_IN: R31.2, R32.2; also elsewhere on the board
V_SEPIC_OUT: R9.2, R16.1; also elsewhere on the board

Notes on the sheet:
I2C ADC
Application note, filter shunt resistor (current measurements). https://www.st.com/resource/en/application_note/an4304-how-to-filter-the-input-of-a-highside-current-sensing-stmicroelectronics.pdf
Sense Amplifier
FSR = ±2.048 V
Resistor values should be equal!
Amplification 50V/V
BETAFLIGHT current
SEPIC current
DRAMCO
I2C ADDR 0x48
Max current 12.81A

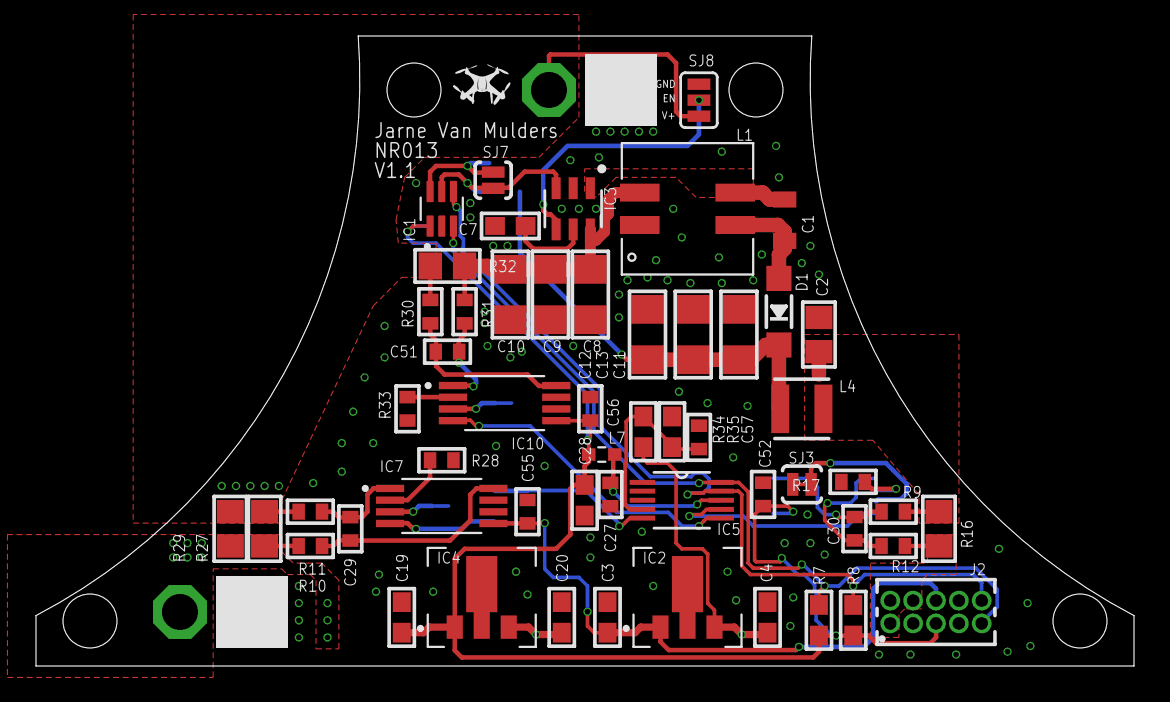
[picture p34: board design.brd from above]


Board: 2 copper layers, 61.0 x 35.0 mm, 65 parts (9 on the bottom side), 35 nets.

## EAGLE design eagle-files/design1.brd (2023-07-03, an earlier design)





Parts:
C1, C2, C5, C7: 10u; 0603
C3, C29: 100n; 0603
C4: LTO; E5-10,5
C6, C12, C13: 100n; 0402
C16: 100p; 0603
C62, C63: 6pF; 0402
C64, C65: 15pF; 0402
C66, C68, C69: 0.1uF; 0402
C67: 4.7uF; 0603
C70, C74: DNP; 0402
C71: 1.0uF; 0402
C72: 0.8pF; 0402
C73: 100pF; 0402
C76, C77: 12p; 0402
CRST: 100n; C0603
D1, D2: SDM03U40; SOD-523
D3: 512-SS24FL; SOD-123
D4: DIODE-SOD323-R; SOD323-R
DEBUG, DEBUG1: CORTEX_DEBUGPTH; 2X5-PTH-1.27MM
IC1: VREG_SOT23; SOT23-R
IC2: STM32L011F3U6TR; QFN50P300X300X60-21N
IC3: TPS54308DDCR; SOT95P280X110-6N
IC4: MCP6486T-E/OT; SOT23-5
IC12: NRF52832; QFN48-6X6MM
JP1, JP2, JP5: JUMPER-SMT_3_NO_NO-SILK; SMT-JUMPER_3_NO_NO-SILK
JP3, JP4: JUMPER-SMT_2_NO_NO-SILK; SMT-JUMPER_2_NO_NO-SILK
L1: 27uH; WE-PD_7332/7345_PLASTIC_BASE
L2: 3.9nH; 0402
L4: 15nH; 0402
L5: 10uH; _0603MP
LED1: LED0805; CHIPLED_0805
LS1, LS2, LS3: MIC94081YFT-TR; IC_MIC94081YFT-TR
Q1: BSS138; SOT23-R
Q2: SI3481DV; TSOP-6.PAC
R1: 220; 0603
R2, R5: 39k; 0603
R3, R4: 1k; 0603
R6, R13, R15: 100k; 0603
R7: R025; 0603
R8: 220k; 0603
R9: 4k7; 0603
R10, R14, R49, R50, R60: 10k; 0603
R11: 56k; 0603
R12: 15k; 0603
R16: 47k; 0603
UART: HEADER-1X3ROUND; 1X03_ROUND
UART_INTERFACE: HEADER-1X4ROUND; 1X04_ROUND
UPDATE: 434111043826
X1: DG3XX-02-5.0; DG306-5.0-02P
X2: ANTENNA_U.FL; U.FL
Y1: 32MHz; CRYSTAL-SMD-2.0X1.6MM
Y2: 32.768kHz; CRYSTAL-SMD-3.2X1.5MM

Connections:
3.3V: C5.1, C6.1, IC1.2 (VOUT), IC4.5 (V+)
!RESET!: CRST.1, DEBUG1.10 (!RESET), IC12.24 (P0.21/RESET), R60.2
ADC1: IC2.8 (PA5), IC12.4 (P0.02/AIN0), JP3.2, R8.2, R9.1
ANT: C72.2, IC12.30 (ANT), L2.2
BUCK-OUT-1: D3.C, R3.2, R7.2
BUCK-OUT-2: JP2.1, LS1.3 (VIN), R4.2, R7.1
BUCK_EN: IC2.14 (PA9), IC12.16 (P0.13), JP1.3
DCC: IC12.47 (DCC), L5.1
DEC4: C71.2, IC12.46 (DEC4), L4.2
DEC5: C69.2, IC12.1 (DEC1)
DEC6: C70.2, IC12.32 (DEC2)
DEC8: C73.2, IC12.33 (DEC3)
EN1: IC2.5 (PA0), IC12.14 (P0.11), LS1.4 (EN)
EN2: IC2.6 (PA1), IC12.15 (P0.12), LS2.4 (EN)
FB: C16.2, D1.K (C), D2.K (C), IC3.4 (FB)
GND: C1.2, C2.2, C4.-, C5.2, C6.2, C7.2, C12.2, C13.2, C16.1, C29.2, C62.1, C63.2, C64.1, C65.1, C66.2, C67.2, C68.2, C69.1, C70.1, C71.1, C72.1, C73.1, C74.2, C76.1, C77.1, CRST.2, D4.A, DEBUG.3 (GND), DEBUG.5 (GND), DEBUG.9 (GNDDTCT), DEBUG1.3 (GND), DEBUG1.5 (GND), DEBUG1.9 (GNDDTCT), IC1.3 (GND), IC2.12 (VSS), IC3.1 (GND), IC4.2 (V-), IC12.31 (VSS), IC12.45 (VSS), IC12.EP (VSS), JP5.1, LED1.C, LS1.2 (GND), LS2.2 (GND), LS3.2 (GND), Q1.2 (S), R2.1, R6.2, R9.2, R10.2, R49.1, UART.3, UPDATE.1, X1.2, X2.1 (GND), X2.2 (GND)
I2C_SCL: IC12.39 (P0.27)
I2C_SDA: C76.2, IC12.38 (P0.26)
LED: IC2.11 (PB1), IC12.18 (P0.15), R1.2
MISO: IC12.41 (P0.29/AIN5)
MOSI: IC12.42 (P0.30/AIN6)
unnamed: JP1.1, R10.1, R13.2
unnamed: C3.1, IC3.6 (BOOT)
unnamed: C3.2, IC3.2 (SW), L1.1
unnamed: Q1.3 (D), R15.2
unnamed: Q2.3 (G), R14.2, R15.1
unnamed: JP5.2, R12.2
unnamed: IC3.5 (EN), JP1.2
unnamed: IC4.4 (-IN), R4.1, R5.1
unnamed: IC4.3 (+IN), R2.2, R3.1
unnamed: Q2.4 (S), R8.1, R14.1, R16.1, X1.1
unnamed: IC2.15 (PA10), JP3.1
unnamed: C2.1, D3.A, L1.2
unnamed: LED1.A, R1.1
unnamed: C74.1, L2.1, X2.3 (SIGNAL)
unnamed: C77.2, IC12.37 (P0.25)
unnamed: L4.1, L5.2
NC: IC12.44 (NC)
NRST: DEBUG.10 (!RESET), IC2.3 (NRST)
P00: C64.2, IC12.2 (P0.00/XL1), Y2.P$2 (2)
P01: C65.2, IC12.3 (P0.01/XL2), Y2.P$1 (1)
P05: IC12.7 (P0.05/AIN3), UART_INTERFACE.3
P06: IC12.8 (P0.06), UART_INTERFACE.2
P07: IC12.9 (P0.07), UART_INTERFACE.4
P08: IC12.10 (P0.08), UART_INTERFACE.1
P09: IC12.11 (P0.09/NFC1)
P10: IC12.12 (P0.10/NFC2)
P16: C29.1, IC12.19 (P0.16), R50.1, UPDATE.2
P20: IC12.23 (P0.20)
P22: IC12.27 (P0.22)
P23: IC12.28 (P0.23)
P24: IC12.29 (P0.24)
P28: IC12.40 (P0.28/AIN4)
PB9: IC2.20 (PB9), R6.1
PG: IC2.7 (PA4), IC12.17 (P0.14), Q1.1 (G)
PWM-CHG: IC12.20 (P0.17), JP5.3
SCK: IC12.43 (P0.31/AIN7)
SWDCLK: DEBUG.4 (SWDCLK/TCK), DEBUG1.4 (SWDCLK/TCK), IC2.17 (PA14), IC12.25 (SWDCLK), R49.2
SWDIO: DEBUG.2 (SWDIO/TMS), DEBUG1.2 (SWDIO/TMS), IC2.16 (PA13), IC12.26 (SWDIO)
SWO/TDO: DEBUG1.6 (SWO/TDO), IC12.21 (P0.18)
USART2_RX: IC2.19 (PB7), UART.1
USART2_TX: IC2.18 (PB6), UART.2
V-ICHG: D1.A, IC2.9 (PA6), IC4.1 (OUT), IC12.6 (P0.04/AIN2), R5.2
V-VCHG: C7.1, D2.A, IC2.10 (PA7), IC12.5 (P0.03/AIN1), R11.1, R12.1
VCHG: C4.+, C12.1, C13.1, DEBUG.1 (VCC), IC2.4 (VDDA), IC2.13 (VDD), JP2.3, JP4.1, LS2.3 (VIN)
VDD-AUX-EN: IC2.1 (PC14)
VDD_BLE: C66.1, C67.1, C68.1, DEBUG1.1 (VCC), IC12.13 (VDD), IC12.36 (VDD), IC12.48 (VDD), JP4.2, LS3.3 (VIN), R50.2, R60.1
VIN: C1.1, IC1.1 (VIN), IC3.3 (VIN), Q2.1 (D), Q2.2 (D), Q2.5 (D), Q2.6 (D), R13.1
VMEAS: JP2.2, LS1.1 (VOUT), LS2.1 (VOUT), R11.2
WAKE-UP: D4.C, IC12.22 (P0.19), R16.2
XC1: C62.2, IC12.34 (XC1(32MHZ)), Y1.3 (2)
XC2: C63.1, IC12.35 (XC2(32MHZ)), Y1.1

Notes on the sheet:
Low Forward Voltage Drop Diode (approx 0.3)
0.596 V
To create stable circuitry Additional diode in needed here 512-SS24FL 40V 2A SCHOTTKY
Additional circuitry required for wake up interrupt trigger Zener diode MM3Z3V0T1G + 47k resistor Connect with PA10
Add digital potentiometer in series with R12 to control output voltage and reduce output power if input voltage is not sufficient enough
Add boot button
These pin could be used for: - informing application MCU, energy storage is charging - informing application MCU, energy storage is fully charger by small pulse
BT Module
Jarne Van Mulders
DRAMCO
NRF52832 (BLE INTERFACE)
Pin 13
Pin 36
Pin 48
nRF52832
32.768kHz Crystal (RTC)
Supply Decoupling
Cortex Debug Connector
nRF52832 Supply Range !1.7 - 3.6V DC!
Add DC/DC converter as power supply for nRF52 nRF will automatically switch between DC/DC and LDO to ensure minimal power consumption
add pull-down to swd-clk to prevent entering debug mode
NRF52832 RXI
NRF52832 TXI
NRF52832 RTS
NRF52832 CTS
MOUSER: 81-LQM18FN100M00D
MOUSER: 609-L-07C15NKV6T
RTS
CTS
UART CONNECTION
Button
ADC
WAKE UP CHECK???


Board: 2 copper layers, 60.0 x 20.0 mm, 79 parts (0 on the bottom side), 59 nets.

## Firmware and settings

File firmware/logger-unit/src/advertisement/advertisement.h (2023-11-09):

#ifndef ADVERTISEMENT_H_
#define ADVERTISEMENT_H_

#include <zephyr/bluetooth/bluetooth.h>
#include <zephyr/bluetooth/hci.h>

// #define STAT_NR				0
// #define VOLT_IN_NR			1
// #define VOLT_OUT_NR 			3
// #define CURR_OUT_NR			5

// #define STAT_CHG			0x00
// #define STAT_RDY			0x01
// #define STAT_NC 			0x02
// #define STAT_CHG_THROTTLED	0x03

#define BT_LE_ADV_CUSTOM BT_LE_ADV_PARAM(0, BT_GAP_PER_ADV_SLOW_INT_MIN, \
					BT_GAP_PER_ADV_SLOW_INT_MAX, NULL)

#define NO_VARIABLES_TX 	5
#define ADV_TX_BUF_LEN 		NO_VARIABLES_TX*2 + 1

extern int16_t uav_battery_voltage_mv;
extern int16_t uav_current_ma;
extern int16_t pre_reg_input_current_ma;
extern int16_t pre_reg_output_current_ma;
extern int16_t vamp_supply_voltage_mv;

// Filter name of incoming ADV messages
static char name [] = "wpt-transmitter";

// *** Default advertisement message content ***
static const struct bt_data ad[] = {
	BT_DATA(BT_DATA_NAME_COMPLETE, name, sizeof(name) - 1),
	//BT_DATA_BYTES(BT_DATA_FLAGS, BT_LE_AD_NO_BREDR)
};

// Default size ADV message
#define DEFAULT_STRUCT_SIZE_ADV_MSG 	sizeof(struct bt_data)
#define DEFAULT_SIZE_ADV_MSG 			(uint8_t)(sizeof(ad)/sizeof(struct bt_data))

// Define struct
struct adv_params {
    bool update;
    uint8_t usr_tx_buffer [ADV_TX_BUF_LEN];
	struct bt_data adv_buffer[DEFAULT_SIZE_ADV_MSG + 1];
};

// // Communication
// static void print_buffer(uint8_t *buffer, uint8_t len){
// 	// Print full message
// 	for (size_t i = 0; i < len; i++) {
//         printk("%02X ", *(buffer + i));
//     }
// 	printk("\n");	
// }



void adv_start();

void adv_change_status(uint8_t stat);

void adv_update_adc_readings(void);


#endif /* ADVERTISEMENT_H_ */

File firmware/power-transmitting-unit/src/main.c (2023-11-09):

/*
 * Copyright (c) 2022 Nordic Semiconductor ASA
 *
 * SPDX-License-Identifier: Apache-2.0
 */

#include <zephyr/sys/printk.h>
#include <zephyr/bluetooth/bluetooth.h>
#include <zephyr/drivers/gpio.h>

#include <zephyr/device.h>
#include <zephyr/devicetree.h>
#include <zephyr/drivers/i2c.h>
// #include <stderr.h>
#include <stdint.h>
#include <stddef.h>

#include "stdio.h"

#include "peripherals/peripherals.h"

#include "advertisement/advertisement.h"

// verplaatsen naar peripherals!!!
#include "adc_update/adc_update.h"

int observer_start(void);

#define LED0_NODE DT_ALIAS(usrled0)	// The devicetree node identifier for the "led0" alias.
// #define LED0_NODE DT_ALIAS(led0)	// The devicetree node identifier for the "led0" alias.


/* STATIC constants */
static const struct gpio_dt_spec led = GPIO_DT_SPEC_GET(LED0_NODE, gpios);

// static int16_t read_channel(uint8_t channel);

extern int16_t channel_voltage [4];

extern int16_t uav_battery_voltage_mv;
extern int16_t uav_current_ma;
extern int16_t pre_reg_input_current_ma;
extern int16_t pre_reg_output_current_ma; 

/* size of stack area used by each thread */
#define STACKSIZE 1024

/* scheduling priority used by each thread */
#define ADC_PRIORITY 8
#define ADV_PRIORITY 7

// *** START THREADS *** //
K_THREAD_DEFINE(start_adc_read_id, STACKSIZE, adc_read_start, NULL, NULL, NULL, ADC_PRIORITY, 0, 0);
K_THREAD_DEFINE(start_adv_id, STACKSIZE, adv_start, NULL, NULL, NULL, ADV_PRIORITY, 0, 0);


extern int16_t three_volt_supply_voltage_mv;
extern int16_t five_volt_supply_voltage_mv;
extern int16_t vamp_supply_voltage_mv;

int main(void)
{
	int err;

	gpio_pin_configure_dt(&led, GPIO_OUTPUT_INACTIVE);		// 

	printk("Start");

	gpio_pin_set_dt(&led, 1);

	/* Initialize the Bluetooth Subsystem */
	err = bt_enable(NULL);
	if (err) {
		printk("Bluetooth init failed (err %d)\n", err);
		return 0;
	}

	
	// gpio_pin_configure_dt(&led, GPIO_OUTPUT_INACTIVE);

	
	gpio_pin_toggle_dt(&led);

    // Start observer *** CURRENTLY DISABLE OBSERVER ***
	// (void)observer_start();

    // Init peripherals (ADS and programmable load)
    perihperals_init();

	// Set prereg on 10V
	peripherals_set_pre_reg_voltage(8000);

	while (1)
	{
		gpio_pin_toggle_dt(&led);
		k_msleep(500);

        peripherals_update_all_ads1115_channels();

		printk("\n");
		printk("uav_battery_voltage_mv: %d\n", uav_battery_voltage_mv);
		printk("uav_current_ma: %d\n", uav_current_ma);
		printk("pre_reg_input_current_ma: %d\n", pre_reg_input_current_ma);
		printk("pre_reg_output_current_ma: %d\n", pre_reg_output_current_ma);

		printk("three_volt_supply_voltage_mv: %d\n", three_volt_supply_voltage_mv);
		printk("five_volt_supply_voltage_mv: %d\n", five_volt_supply_voltage_mv);
		printk("vamp_supply_voltage_mv: %d\n", vamp_supply_voltage_mv);

        // for(int i = 0; i < ADS1115_NUMBER_OF_CHANNELS; i++){
        //     //printk("Channel %d: %d mV\n", i, channel_voltage[i]);

		// 	printk("Res %d: %d mV\n", i, channel_result [i]);
		// }

        // test res
        // TPL0401x_update_resistance(100);

        // peripherals_set_pre_reg_voltage(10000);
        
        // k_msleep(2000);
        
        // peripherals_set_pre_reg_voltage(5000);

        // test res
        // TPL0401x_update_resistance(25);

	}


	printk("Exiting %s thread.\n", __func__);
	return 0;
}

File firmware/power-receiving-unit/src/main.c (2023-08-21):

/*  ____  ____      _    __  __  ____ ___
 * |  _ \|  _ \    / \  |  \/  |/ ___/ _ \
 * | | | | |_) |  / _ \ | |\/| | |  | | | |
 * | |_| |  _ <  / ___ \| |  | | |__| |_| |
 * |____/|_| \_\/_/   \_\_|  |_|\____\___/
 *                           research group
 *                             dramco.be/
 *
 *  KU Leuven - Technology Campus Gent,
 *  Gebroeders De Smetstraat 1,
 *  B-9000 Gent, Belgium
 *
 *         File: main.c
 *      Created: 2023-06-30
 *       Author: Jarne Van Mulders
 *      Version: major.minor
 *
 *  Description: wpt-receiver
 *      IoT node & wpt receiver
 *
 *  Commissiond by PhD
 */

#include <inttypes.h>
#include <stddef.h>
#include <stdint.h>

// #include <zephyr/types.h>
// #include <zephyr/sys/printk.h>
// #include <zephyr/sys/util.h>
// #include <zephyr/kernel.h>
// #include <zephyr/device.h>
// #include <zephyr/drivers/gpio.h>
// #include <zephyr/sys/__assert.h>
// #include <string.h>

// // // ADC includes
// #include <zephyr/devicetree.h>
// #include <zephyr/drivers/adc.h>

// SLEEP includes
// #include <stdio.h>
// #include <zephyr/init.h>
// #include <zephyr/pm/pm.h>
// #include <zephyr/pm/device.h>
// #include <zephyr/pm/policy.h>
// #include <soc.h>
// #include <hal/nrf_gpio.h>

/* Custom libs include */
#include "advertisement/advertisement.h"
#include "adc_update/adc_update.h"
#include "state_machine/state_machine.h"
#include "gpio_control/gpio_control.h"


/* size of stack area used by each thread */
#define STACKSIZE 1024

/* scheduling priority used by each thread */
#define ADV_PRIORITY 7
#define ADC_PRIORITY 8


// *** START THREADS *** //
K_THREAD_DEFINE(start_adv_id, STACKSIZE, adv_start, NULL, NULL, NULL, ADV_PRIORITY, 0, 0);
K_THREAD_DEFINE(start_adc_read_id, STACKSIZE, adc_read_start, NULL, NULL, NULL, ADC_PRIORITY, 0, 0);
K_THREAD_DEFINE(start_sm_id, STACKSIZE, sm_start, NULL, NULL, NULL, 6, 0, 0);
K_THREAD_DEFINE(led_blink_id, STACKSIZE, led_blink_start, NULL, NULL, NULL, 9, 0, 0);


// General error
int err;


// *** MAIN *** //
int main(void)
{
	// Start
	printk("Start firmware\n");

	// *** SETUP FUNCTIONS *** //
	// gpio_pin_configure_dt(&led, GPIO_OUTPUT_INACTIVE);			// Default LED off
	// gpio_pin_configure_dt(&ls_en_2, GPIO_OUTPUT_INACTIVE);		// Default load switch disabled (no leakage current to charger circuit)
	// gpio_pin_configure_dt(&pg, GPIO_OUTPUT_INACTIVE);			// Default voltage WPT receiver blocked
	// gpio_pin_configure_dt(&buck_en, GPIO_OUTPUT_INACTIVE);		// 
	// gpio_pin_configure_dt(&sens_en, GPIO_OUTPUT_INACTIVE);		// 

	setup_pins();

	// gpio_pin_set_dt(&sens_en, 0);

	// K_SYSCALL_LED_BLINK

	// led_set_brightness(&led_pin, &led_pin, 0);


	// *** Configure to generate PORT event (wakeup) on button 1 press. *** //
	// !!! >>>usrbutton0<<< NEED TO BE CHANGED TO >>>wakeup1<<< !!! //
	nrf_gpio_cfg_input(NRF_DT_GPIOS_TO_PSEL(DT_ALIAS(wakeup1), gpios), NRF_GPIO_PIN_PULLDOWN);
	nrf_gpio_cfg_sense_set(NRF_DT_GPIOS_TO_PSEL(DT_ALIAS(wakeup1), gpios), NRF_GPIO_PIN_SENSE_HIGH);
	nrf_gpio_cfg_input(NRF_DT_GPIOS_TO_PSEL(DT_ALIAS(usrbutton0), gpios), NRF_GPIO_PIN_PULLUP);
	nrf_gpio_cfg_sense_set(NRF_DT_GPIOS_TO_PSEL(DT_ALIAS(usrbutton0), gpios), NRF_GPIO_PIN_SENSE_LOW);

	// *** To read supply voltage, load switch 2 should be enabled. ***
	// gpio_pin_set_dt(&ls_en_2, 1);

	// gpio_pin_set_dt(&pg, 1);

	// gpio_pin_set_dt(&buck_en, 1);


	// *** MAIN LOOP *** //
	while(1){

		// Print readed values
		printk("--------------------------------------------\n");
		printk("input_voltage_mv: %"PRId32" mV\n", input_voltage_mv);
		printk("supply_voltage_mv: %"PRId32" mV\n", supply_voltage_mv);
		printk("buck_current_ma: %"PRId32" mA\n", buck_current_ma);
		printk("Current state = %d \n", current_state);
		// printk("Pulse value = %d \n", pulse_width_value);

		k_msleep(1000);

		// pin_toggle(&led_pin);

		// change_pwm_pulse_size(2);

		// k_msleep(3000);

		// change_pwm_pulse_size(100);

		// pin_set(&ls_en_1_pin);
		// pin_set(&ls_en_2_pin);

		// k_msleep(3000);

		// pin_reset(&ls_en_1_pin);
		// pin_reset(&ls_en_2_pin);

	}

	return 0;
}

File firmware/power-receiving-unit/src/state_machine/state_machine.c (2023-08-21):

#include "state_machine.h"

// *** Variables *** //
uint16_t timer_check = 0;
state_type current_state = INIT;

uint8_t pulse_width_value = PID_UPPER_THRESHOLD;
uint8_t check = 0;

SYS_INIT(disable_ds_1, PRE_KERNEL_2, 0);

void Enable_buck_converter(void){
	printk("Enable BUCK\n");
    pin_set(&ls_en_1_pin);
    pin_set(&ls_en_2_pin);
	k_msleep(50);
	pin_set(&pg_pin);
	k_msleep(50);
	pin_set(&buck_en_pin);

}

void Disable_buck_converter(void){
	printk("Disable BUCK\n");
	pin_reset(&buck_en_pin);
	k_msleep(50);
	pin_reset(&pg_pin);
	k_msleep(50);
	pin_reset(&ls_en_1_pin);
  pin_reset(&ls_en_2_pin);
}

void state_machine(void){
    
    //	Check input voltage exceed max voltage
	if(input_voltage_mv > MAX_VOLTAGE){
      current_state = OVER_VOLTAGE;
    }

    // Check input voltage in not below minimum voltage
    if(input_voltage_mv < SLEEP_VOLTAGE){
      current_state = SLEEP;
    }

    switch (current_state){
      /*******************************************************************************************/
      case INIT: //0

        // No charging may occur in the INIT phase
        Disable_buck_converter();

        // Reset pulse_width_value
        #ifdef PWM_ENABLE
            pulse_width_value = PID_INIT;
        #endif

        // Check input voltage before start charging
        if(input_voltage_mv < MAX_VOLTAGE && input_voltage_mv > MIN_VOLTAGE){
          current_state = START_CHARGING;
          break;
        }

        // Blink led
        change_blink_delay(500, 500);
      break;
      /*******************************************************************************************/
      case START_CHARGING: //1
        // Enable buck converter safely
        Enable_buck_converter();

        printk("Start charging!");

        change_pwm_pulse_size(0);

        k_msleep(100);

        printk("Current = %d \n", buck_current_ma);

        if(buck_current_ma > MIN_CURRENT && buck_current_ma < 1000){
            // Change state
            current_state = CHARGING;
            printk("Current state changed");
        }

        printk("Current state = %d \n", current_state);

      break;
      /*******************************************************************************************/
      case CHARGING: //2

        // Blink led
        change_blink_delay(100, 900);
        
        #ifdef PWM_ENABLE
            if(check == 5){
                // Check input voltage with PID controller
                pulse_width_value = pwm_value_controller(input_voltage_mv, pulse_width_value);

                // Compensate programmable potentiometer
                change_pwm_pulse_size(pulse_width_value);
                check = 0;
            }
            check++;
        #endif

        // If under voltage occurs, wait for enough voltage to resume
        if(input_voltage_mv < MIN_VOLTAGE){
          current_state = INIT;
          break;
        }

        // Check every 10 seconds if current is lower then MIN_CURRENT and voltage reached target level.
        if(buck_current_ma < MIN_CURRENT && timer_check > 10*1000 && supply_voltage_mv > MIN_CHARGE_CUTTOF_VOLTAGE){
          timer_check = 0;
          current_state = STOP_CHARGING;
        }

        timer_check++;

      break;
      /*******************************************************************************************/
      case STOP_CHARGING: //3

        // Disable buck conveter safely
        Disable_buck_converter();

        // Reset pulse_width_value
        #ifdef PWM_ENABLE
            pulse_width_value = PID_INIT;
        #endif

        // TODO SEND MESSAGE TO TRANSMITTER

        // if(buck_current_ma < MIN_CURRENT && supply_voltage_mv > MIN_CHARGE_CUTTOF_VOLTAGE){
        //   current_state = SLEEP;
        // }
        // else{
        //   current_state = INIT;
        // }
        current_state = SLEEP;
      break;
      /*******************************************************************************************/
      case OVER_VOLTAGE: //4

        // Blink led
        change_blink_delay(100, 100);

        // Disable buck conveter safely
        Disable_buck_converter();

        // Check for safe voltage
        if(input_voltage_mv < MAX_VOLTAGE){
          current_state = INIT;
        }
      break;
      /*******************************************************************************************/
      case SLEEP: //5

	  	// To be really sure, disable buck converter
		Disable_buck_converter();

		printk(" *** I am going to sleep! *** \n");
        
        k_msleep(1000);

        // ??? Disable all threads ???

        // Disable USER LED
       	pin_reset(&led_pin);

        // ??? Check if input voltage is above 2 V and enable timer interrupt ???

        // ??? Reconfigure GPIO pins for sleep mode: EN1_Pin EN2_Pin PG_Pin BUCK_EN_Pin ???

		#ifdef DEEP_SLEEP_ENABLE
			/* Force entry to deep sleep on any delay. */
			pm_state_force(0u, &(struct pm_state_info){PM_STATE_SOFT_OFF, 0, 0});

			/* Go to sleep. Idle thread keeps running. */
			k_sleep(K_SECONDS(SLEEP_S));
		#endif

        // Change state
        current_state = INIT;

      break;
      /*******************************************************************************************/
      default:
      current_state = INIT;
      break;
    }
}

// Loop
void sm_start(void){

    // Wait for other threads to start up
    k_msleep(1000);

    while(1){
        k_msleep(100);
        state_machine();
    }
}

/* Prevent deep sleep (system off) from being entered on long timeouts
 * or `K_FOREVER` due to the default residency policy.
 *
 * This has to be done before anything tries to sleep, which means
 * before the threading system starts up between PRE_KERNEL_2 and
 * POST_KERNEL.  Do it at the start of PRE_KERNEL_2.
 */

uint8_t disable_ds_1(void){
	pm_policy_state_lock_get(PM_STATE_SOFT_OFF, PM_ALL_SUBSTATES);
	return 0;
}

static uint8_t pwm_value_controller(int32_t measured_value, uint8_t value){

    if(measured_value < 0){
        return PID_UNDER_THRESHOLD;
    }

    if(measured_value > PID_SETPOINT){
        value--;
    }
    else{
        // uint16_t res = (PID_SETPOINT - measured_value)/1000;
        // value = value - res;
        value++;
    }

    if(value > PID_UPPER_THRESHOLD){value = PID_UPPER_THRESHOLD;}
    if(value < PID_UNDER_THRESHOLD){value = PID_UNDER_THRESHOLD;}

    return value;
}

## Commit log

2023-06-29 Add PCB files
    [design1.brd, design1.sch]
2023-06-29 Add observer filter
2023-07-02 kicad files
    [design1.sch, kicad-pcb-files.kicad_pcb, kicad-pcb-files.kicad_sch]
2023-07-03 update pcb + test ltspice
    [design1.sch]
2023-07-03 update pcb
    [design1.brd, design1.sch]
2023-07-04 draft scheme power-receiving-unit
    [design1.brd, design1.sch, kicad-pcb-files.kicad_pcb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]
2023-07-04 trying to get ADC working
2023-07-18 power receiving unit PCB V1.0 ready
    [design1.GBL, design1.GBO, design1.GBP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]
2023-07-20 ADC reads successfully added and tested
    [design1.sch]
2023-07-20 adc lib + deep sleep added
2023-08-07 Continued to work on design PTU
    [design1.sch]
2023-08-09 ltspice buck-boost
    [design1.brd, design1.sch]
2023-08-09 Update HW PTU
    [design1.brd, design1.sch]
2023-08-16 Update SW PRU & HW PRU + PTU
    [design.brd, design.sch, design1.brd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]
2023-08-21 Update PRU HW + firmware (send pru info via BLE adv)
    [design1.brd, design1.sch]
2023-09-01 Update hardware PTU
    [design.GBL, design.GBO, design.GBP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]
2023-09-01 Add ptu board file
2023-09-01 Update PTU firmware and hardware
    [design.sch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]
2023-09-13 Update PTU firmware
    Add ADS1115 library
    [design1.brd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]
2023-09-21 Update firmware PSU (PTU) board (soldering and testing)
    [design.GBL, design.GBO, design.GBP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]
2023-09-27 Update firmware and reorganization folders
    [design.GBL, design.GBO, design.GBP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]
2023-10-20 Update firmware - hardware all
    [design1.brd, design1.sch]
2023-10-20 Update PRU board dts file
2023-11-09 Update firmware logger + add python scripts
    [CouplingCoeff-InitialTest50-200mm.csv, CouplingCoeff-XYZmove-missing-values-added.csv, CouplingCoeff-XYZmove.csv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]
2023-11-14 update scripts
    [CouplingRX2.csv, CouplingRX2.xlsx, k_RX2_ifv_angle.csv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]
2023-11-20 Last updates before paper submission
    [(k_ifv_RX).xlsx, L_coupled.xlsx]

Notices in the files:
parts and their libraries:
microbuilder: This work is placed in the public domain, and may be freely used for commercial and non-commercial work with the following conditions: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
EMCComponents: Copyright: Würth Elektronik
